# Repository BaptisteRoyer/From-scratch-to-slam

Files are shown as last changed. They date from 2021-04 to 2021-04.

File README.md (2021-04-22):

# From Scratch to SLAM

From scratch to SLAM est un projet open Source, créé par 4 étudiants de Junia ISEN. Dans ce repository vous trouverez tous les documents nécessaires afin de faire fonctionner votre robot.

Il est nécessaire pour tout commencer de télécharger le fichier notice.pdf.

Voici comment sont rangés nos fichiers :

- Dans le dossier Électronique, vous trouverez tout ce qui concerne les PCBs, le schéma électrique, et les datasheets des différents composants du projet
- Dans le dossier Pièces 3D, vous trouverez les fichiers 3Ds bruts des différents composants, cela vous permettra de redimensionner les différentes parties de votre robot.
- Dans le dossier Impression 3D, vous trouverez les fichiers stl à slicer, afin d'imprimer en 3D les pièces du robot.
- Dans le dossier Découpe Laser, vous trouverez tous les fichiers à découper, ce sont les plaques de plexiglass.
- Dans le dossier Software, vous trouverez des petits programmes de démonstration.

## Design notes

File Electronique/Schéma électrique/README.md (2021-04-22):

- La breadboard n'est pas représente sur le schéma (les pont en H sont branchés dessus ainsi que les masses de chaque bumper). 
- Le PCB couronne pour les capteurs IR n'est pas représenté sur le schéma.
- La batterie a les caractéristiques suivantes : 11.1 V, 5Ah, 50C.

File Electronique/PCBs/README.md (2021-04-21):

Vous trouverez dans ces dossiers les fichiers de conception (PCB et schémas électroniques)
et les fichiers d'impression (Gerber et NC Drill) des pièces PCB nécessaires aux bumpers et
aux capteurs IR.

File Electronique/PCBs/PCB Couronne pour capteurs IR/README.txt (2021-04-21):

La couronne pour les capteurs IR est divisée en deux, vous trouverez les deux parties dans ce dossier.

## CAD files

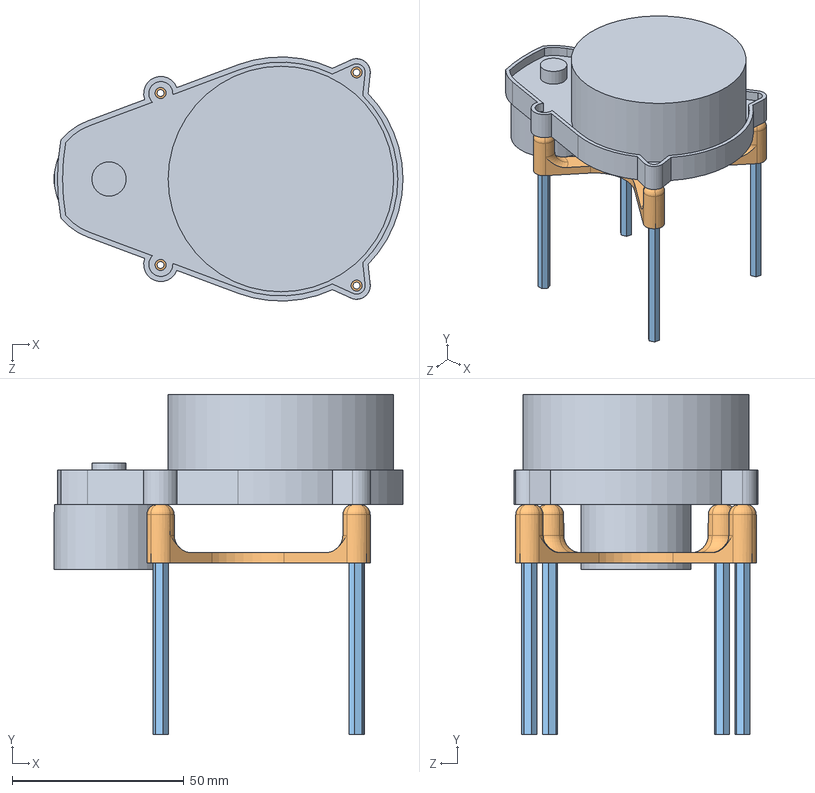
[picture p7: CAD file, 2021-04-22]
Pièces 3D/SolidWorks/lidar pilotis.SLDASM
101.5 x 99.0 x 70.9 mm
ydlidar x4
raccord lidar
support_hex60 x 4

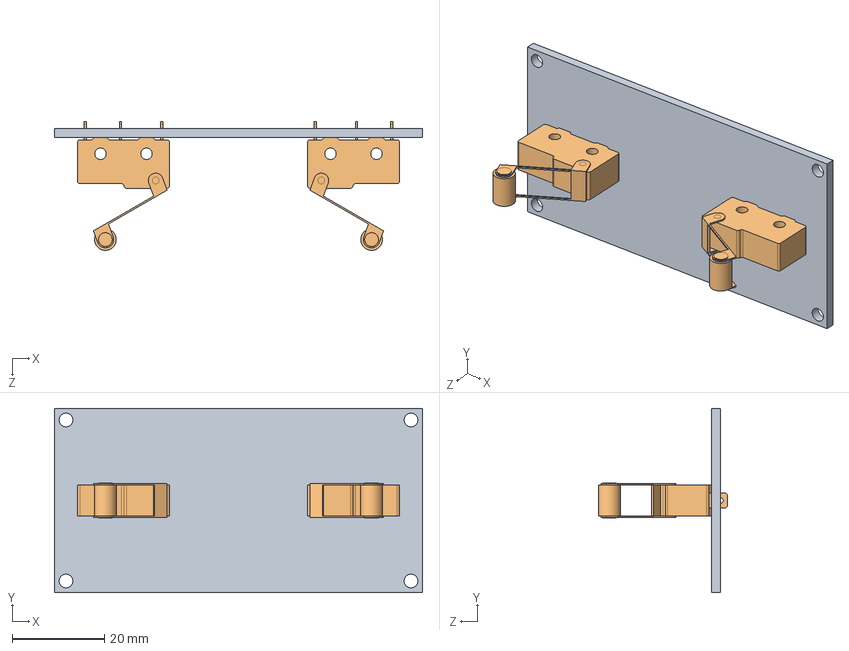
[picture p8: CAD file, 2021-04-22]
Pièces 3D/SolidWorks/pcb_bumper.SLDASM
80.0 x 40.0 x 28.0 mm
pcb_interrupteur
microswitch x 2

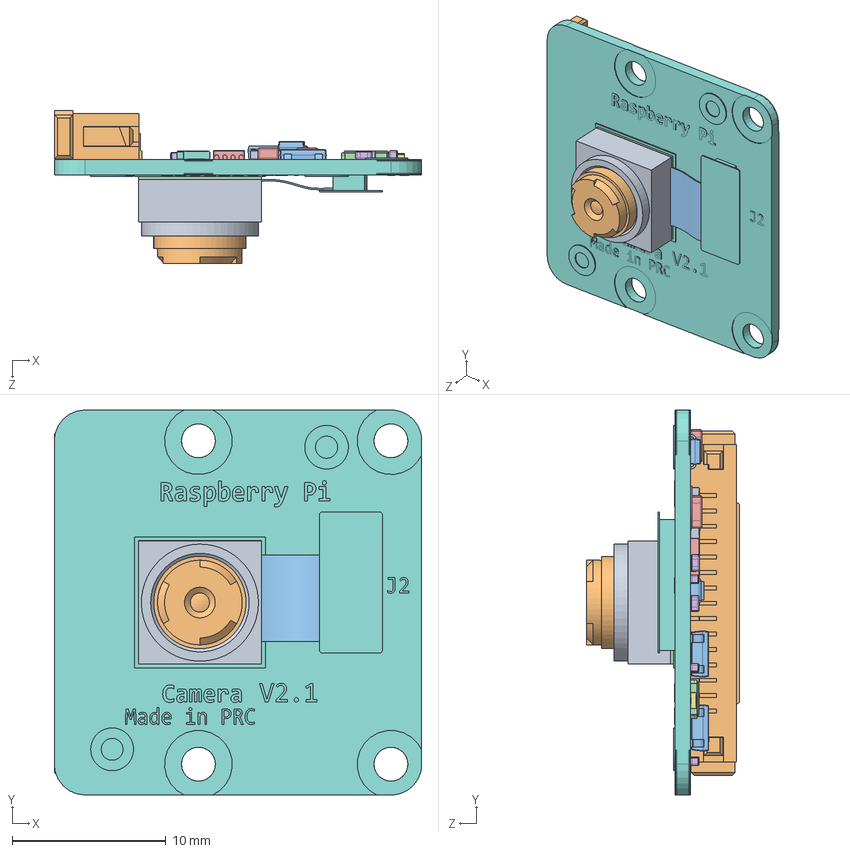
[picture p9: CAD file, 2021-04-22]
Pièces 3D/SolidWorks/RspCameraMia.SLDASM
23.9 x 25.0 x 9.96 mm
70521906_01.stp
70521906_02.stp
70521906_03.stp
70521906_04.stp
70521906_05.stp
70521906_06.stp
70521906_07.stp
PicameraPCB.stp
OVA5647_Housing.stp
OVA5647_Lens_FOV.stp
ribbon_cam.stp
CCD.stp
CAPC-0805-T0.75-BN.stp x 2
CAPC-0402-T0.55-BN.stp x 10
RESC-0402.stp x 3
RESC-0603.stp x 2
RESC-1210.stp
c-1-1734248-5-e-raspberry_display.stp
SOT23-5.stp x 3
KX7 SMD Quartz Crystal Resonator 3.2x2.5mm.stp
c6aaa.stp
4pin_smd.stp x 3

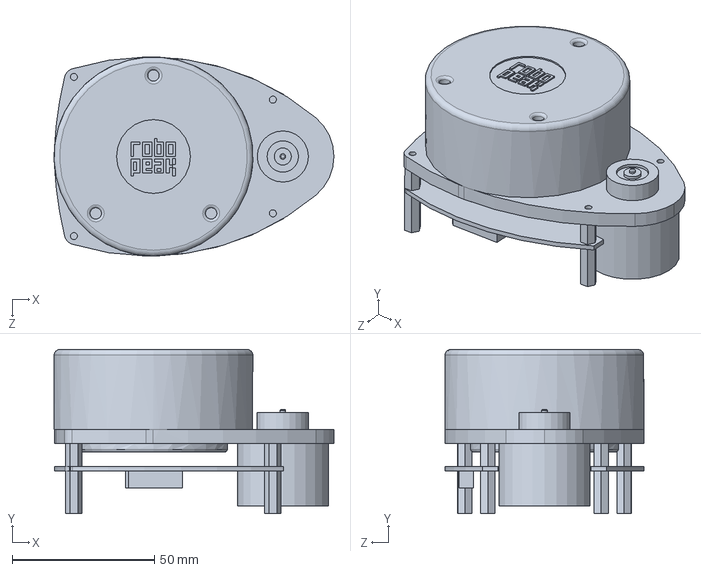
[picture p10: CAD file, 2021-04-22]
Pièces 3D/SolidWorks/rplidar_main.SLDPRT
98.5 x 57.7 x 70.0 mm

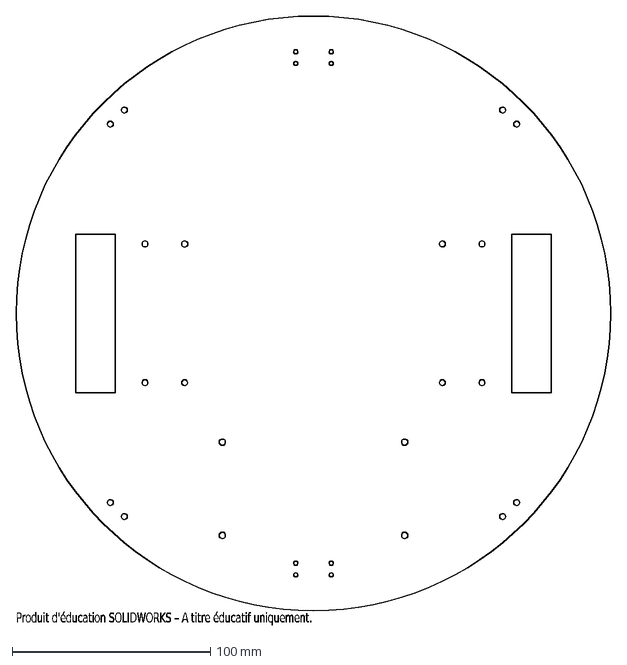
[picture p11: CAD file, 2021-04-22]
Découpe laser/base_300mm.DXF
Produit d'éducation SOLIDWORKS – A titre éducatif uniquement.

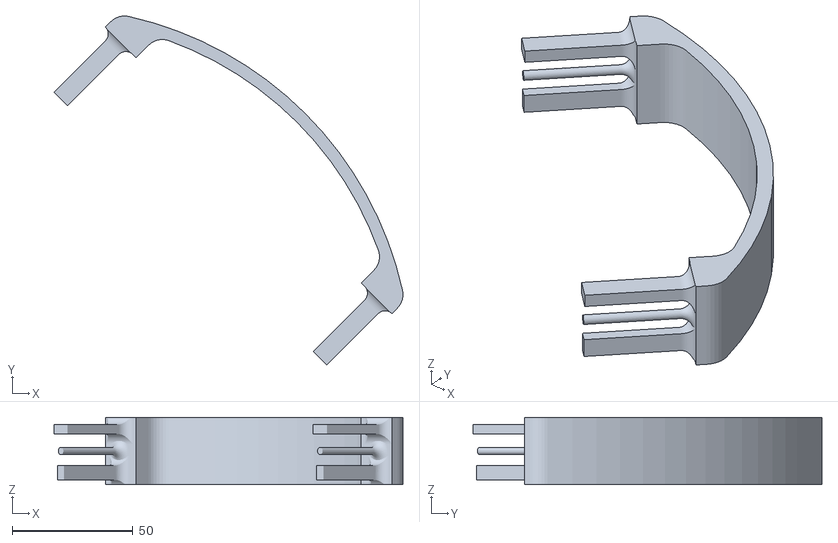
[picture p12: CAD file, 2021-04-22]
Impression 3D/bumper.STL
144.8 x 144.8 x 28.0

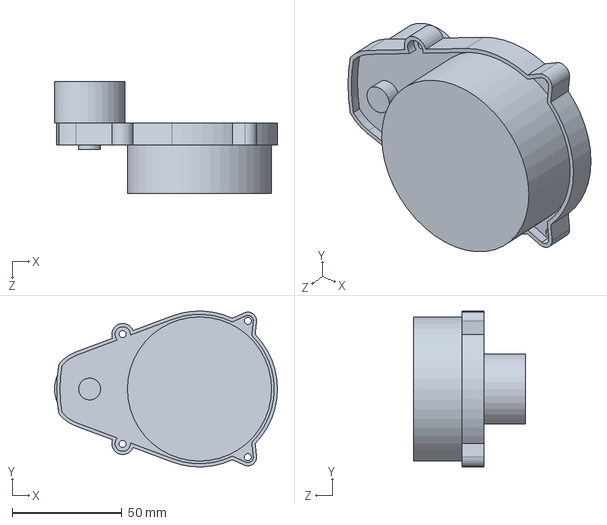
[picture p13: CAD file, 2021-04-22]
Pièces 3D/SolidWorks/ydlidar x4.SLDPRT
101.5 x 70.9 x 51.0 mm

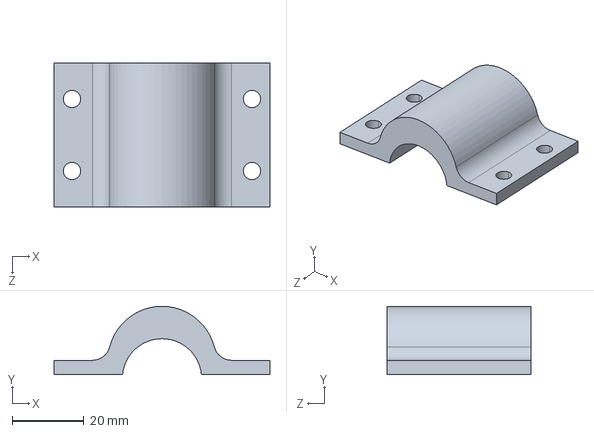
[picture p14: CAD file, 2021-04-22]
Pièces 3D/Step/mors_moteur_amovible.STEP
60.0 x 19.0 x 40.0 mm

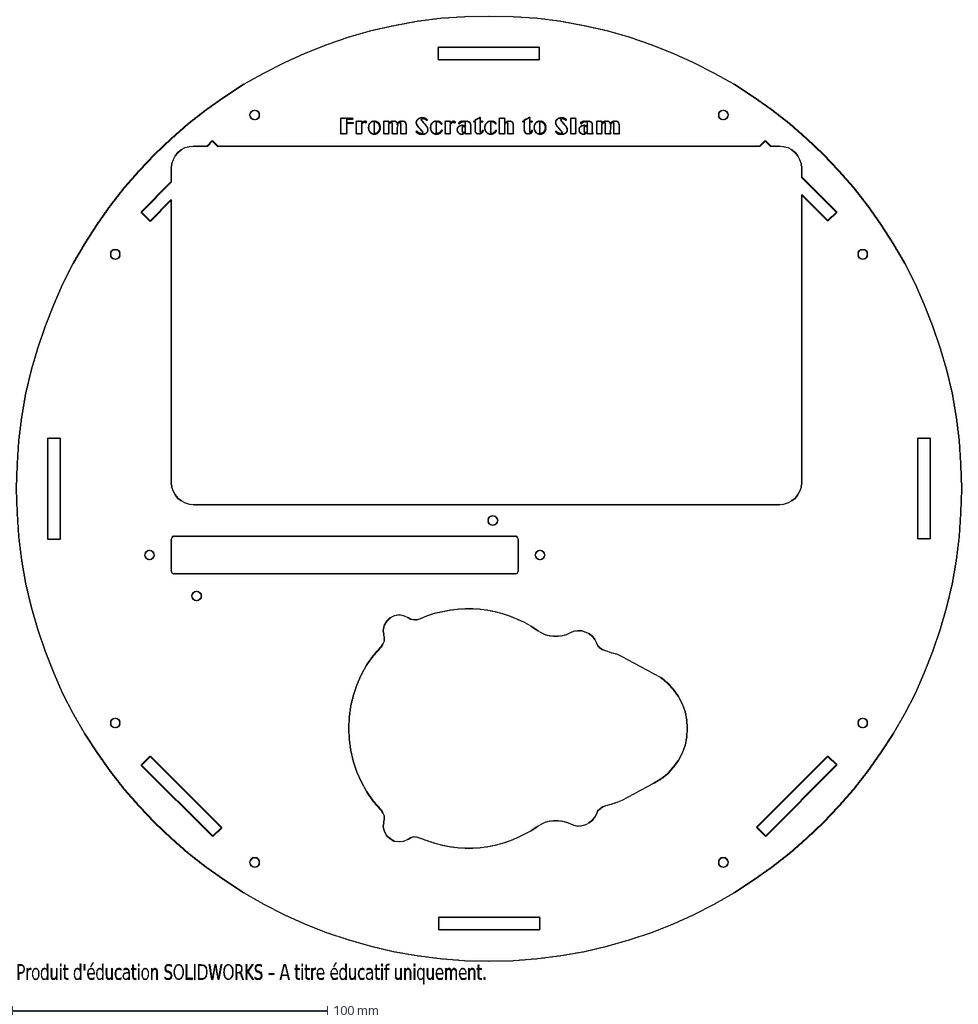
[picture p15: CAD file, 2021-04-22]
Découpe laser/capot.DXF
Produit d'éducation SOLIDWORKS – A titre éducatif uniquement.

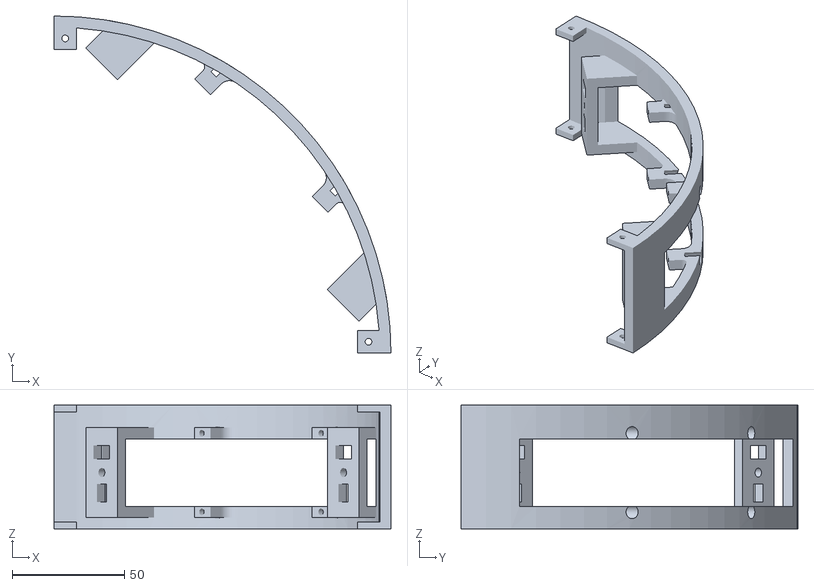
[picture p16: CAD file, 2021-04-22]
Impression 3D/paroi_bumper.STL
150.0 x 150.0 x 55.0

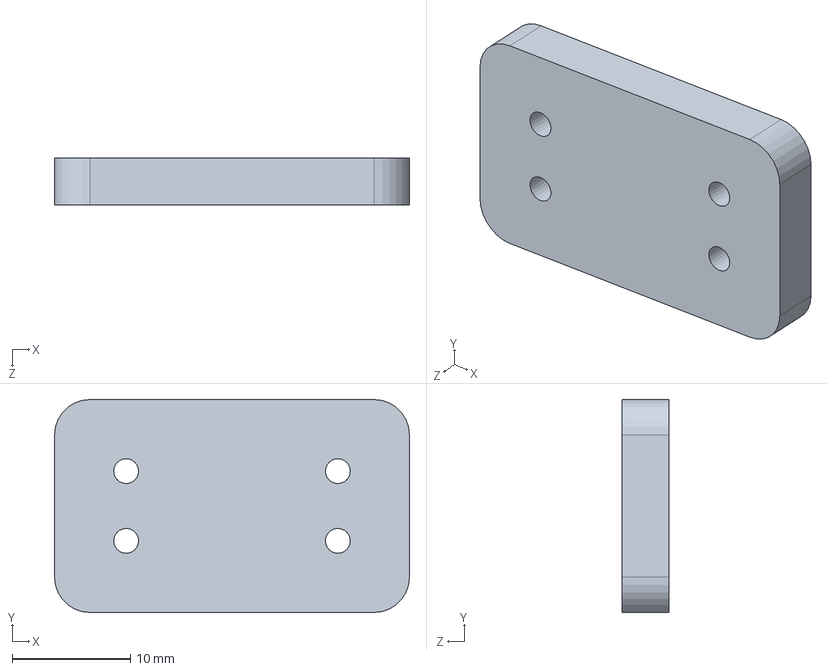
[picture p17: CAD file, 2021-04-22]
Pièces 3D/SolidWorks/support_roulement_a_bille.SLDPRT
30.0 x 18.0 x 4.00 mm

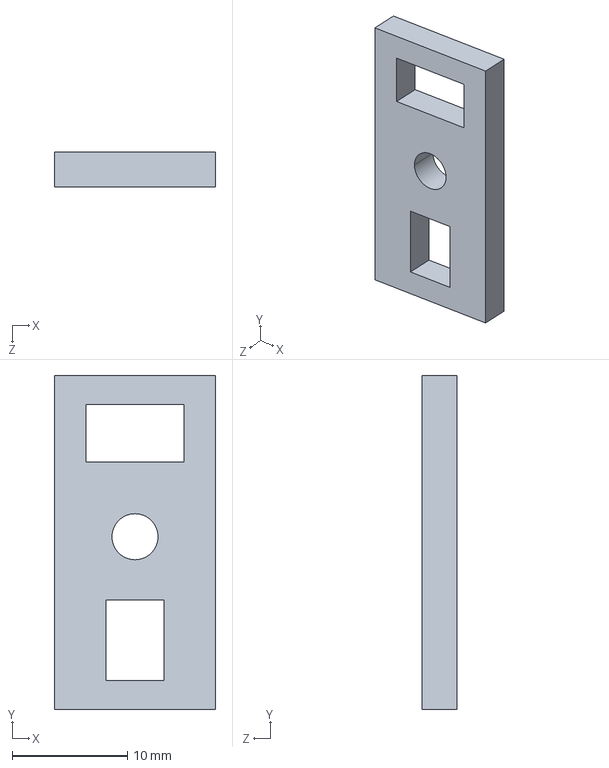
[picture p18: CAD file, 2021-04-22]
Pièces 3D/Step/bloqueur_bumper.STEP
14.0 x 29.0 x 3.00 mm

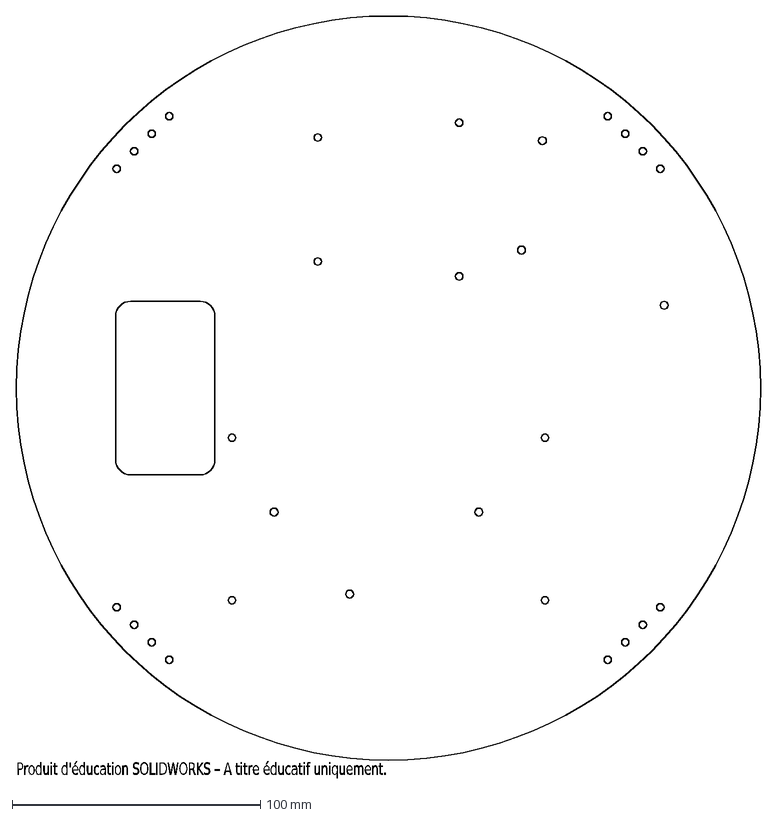
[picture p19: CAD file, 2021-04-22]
Découpe laser/support_cartes.DXF
Produit d'éducation SOLIDWORKS – A titre éducatif uniquement.

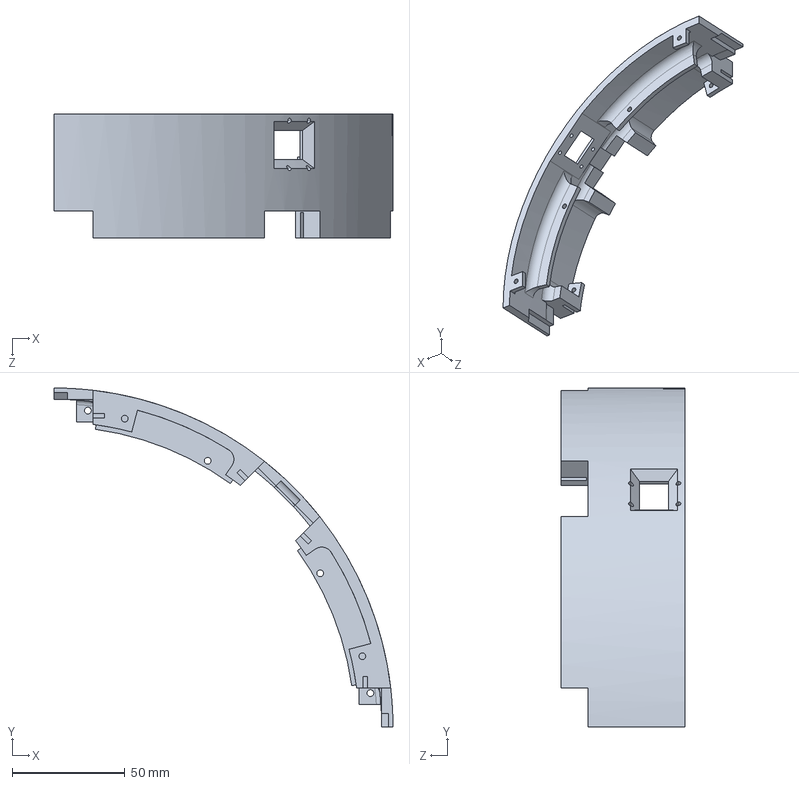
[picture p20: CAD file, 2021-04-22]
Pièces 3D/Step/quart_paroi_superieur_camera.STEP
150.0 x 150.0 x 55.0 mm

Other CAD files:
Pièces 3D/SolidWorks/raspberrypi_b_+_(assembly).SLDASM
Impression 3D/mors_moteur_amovible.STL
Impression 3D/mors_moteur_fixe.STL
Pièces 3D/SolidWorks/blindage_moteur.SLDPRT
Impression 3D/bloqueur_bumper.STL
Impression 3D/paroi_bouton.STL
Impression 3D/paroi_camera.STL
Impression 3D/paroi_superieure_laterale.STL
Impression 3D/raccord lidar.STL
Impression 3D/support_hub_USB.STL
Pièces 3D/SolidWorks/Capteur IR.SLDPRT
Pièces 3D/SolidWorks/Capteur IR.STEP
Pièces 3D/SolidWorks/Capteur IR.x_t
Pièces 3D/SolidWorks/MPU 6050 IMU.STEP
Pièces 3D/SolidWorks/Raspberry Pi 3 Model B+ Reference Model.step
Pièces 3D/SolidWorks/Raspberry Pi Display V1.1.SLDASM
Pièces 3D/SolidWorks/Raspberry Pi Display V1.1.STEP
Pièces 3D/SolidWorks/Switch Button.SLDPRT
Pièces 3D/SolidWorks/base.SLDPRT
Pièces 3D/SolidWorks/batterie.SLDPRT
Pièces 3D/SolidWorks/bloqueur_bumper.SLDPRT
Pièces 3D/SolidWorks/bumper.SLDPRT
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

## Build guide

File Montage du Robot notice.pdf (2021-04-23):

FROM SCRATCH TO SLAM – ROYER / MAERTEN / CANDUSSO / HAGUET | 1

# Notice d’assemblage

From Scratch to Slam

## Table des matières

## Liste du matériel :

- 3 plaques de plexiglas 32x32 cm minimum PMMA 5mm
- 1 bobine de plastique PLA
- Pack 100 boulons M3
- 8 vis auto-taraudeuses M4.8
- 12 boulons M2 nylon (boulon = ensemble vis + écrou)

Liste des composants & pièces :

1

er Etage :

- Base (plaque plexiglas)
- Carte Open UPS
- 2 moteurs Digilent 6V
- Batterie 12V
- 8 interrupteurs bumper
- 4 pcb interrupteurs bumper
- 4 parois bumper
- 4 bumpers
- 8 ressorts
- 2 modules mors moteur (pièce fixée à la base + pièce supérieure)
- 1 support de roue folle
- 1 roue folle (à bille)

2

e Etage :

- Support cartes (plaque plexiglas)
- 2 cartes Arduino Due
- ½ breadboard
- 2 hacheurs
- IMU
- Lidar
- Raccord lidar
- 8 colonnettes 55 mm
- Carte Raspberry Pi 4 model B
- Caméra RPi 8 Mpixels
- 8 capteurs IR
- Couronne PCB capteurs IR (2 pièces)
- Ecran tactile RPi 7 pouces
- 1 paroi supérieure caméra
- 1 paroi supérieure boutons
- 2 parois supérieures latérales
- Capot (plaque plexiglas)

## 1. Arborescence

Les fichiers sont enregistrés comme suit dans le Github du projet.

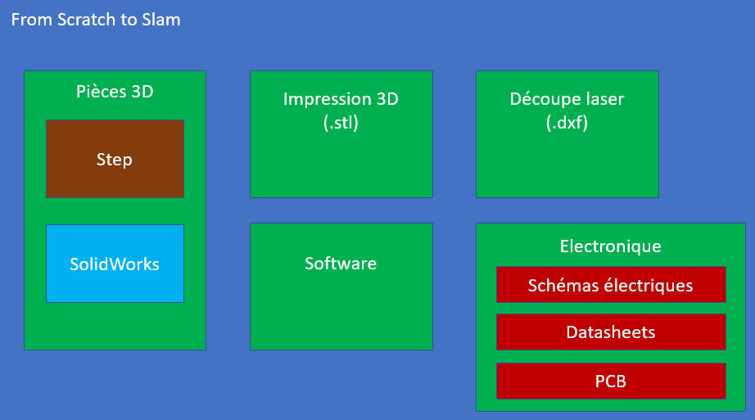
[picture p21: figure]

Les pièces 3D sont enregistrées au format .step et au format .sldprt (Solidworks 2019) pour pouvoir les ouvrir selon le logiciel de CAO utilisé. A noter : on ne peut pas ouvrir une pièce Solidworks éditée sur une version future.

### 1. Impression 3D

Les fichiers d’impression sont enregistrés au format .stl pour les ouvrir sur un logiciel d’impression 3D (ex. PrusaSlicer). On place les pièces sur le logiciel de manière optimale (pour éviter trop de supports et prendre le moins de temps d’impression) puis on en retire un fichier .gcode que l’imprimante lit.

### 2. Découpe laser

Les fichiers de découpe sont enregistrés au format .dxf pour les ouvrir sur un logiciel de découpe laser (ex. Job control Trotec). On détermine l’ordre de tracé du laser sur le logiciel et on lance la découpe.

Tous les fichiers concernant les schémas électriques et les PCB correspondants sont dans le dossier Electronique ainsi que les datasheets des composants utilisés.

## 2. Assemblage

Pour imprimer, découper et assembler le robot, on partira du bas vers le haut car on souhaite mettre en œuvre en premier les commandes moteur. Aussi on a choisi de coller les écrous sur les parois afin de visser plus facilement.

1. Découper au laser la base.dxf dans le dossier Découpe laser.

& imprimer dans le dossier impression 3D

- 2 mors_moteur_fixe.stl
- 2 mors_moteur_amovible.stl
- 4 bumpers.stl
- 4 paroi_bumper.stl
- 8 bloqueur_bumper.stl
- 1 support_roulement_a_bille.stl

& découper les PCB interrupteurs

2. Souder les interrupteurs sur les PCB correspondants
3. Visser les PCB interrupteurs sur les parois

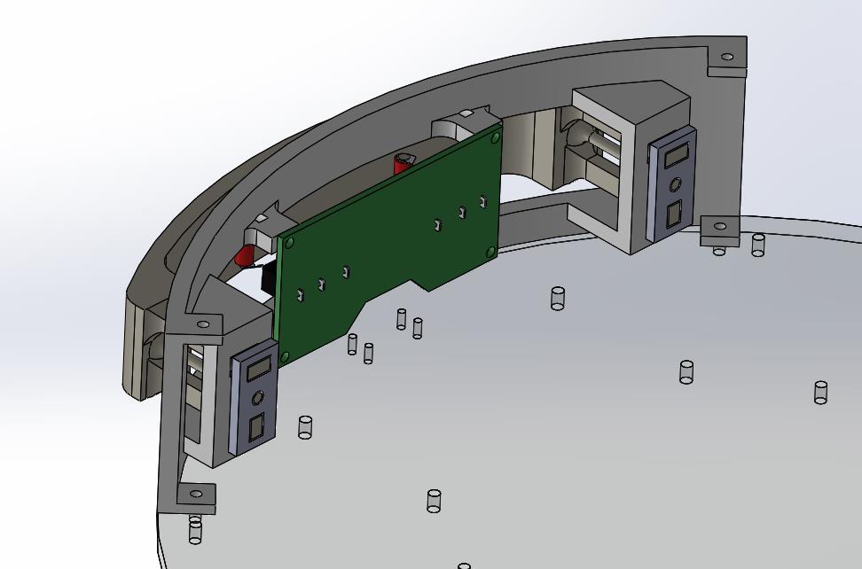
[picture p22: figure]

Figure 1 assemblage paroi bumper bloqueur et PCB interrupteur

4. Placer les ressorts sur les bumpers et les assembler sur les parois puis coller les bloqueurs sur les bumpers de sorte que les interrupteurs effleurent les bumpers.

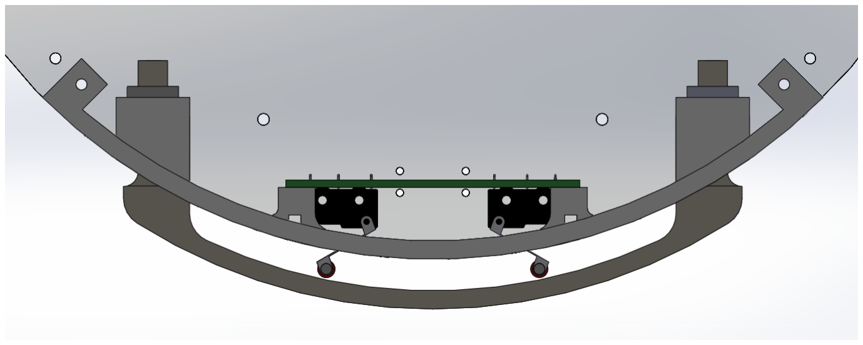
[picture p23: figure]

Figure 2 Assemblage bumper

5. Assembler les mors moteur en y insérant les moteurs digilent 6V (limer légèrement au besoin & 8 vis auto-taraudeuses M4.8)
6. Visser la roue folle et le support contre la base (4 vis nylon et écrou métal M2)
7. Visser les mors moteurs sur la base (8 boulons M3)
8. Visser la carte Open UPS (8 boulons M3)
9. Visser les parois bumper assemblées (8 boulons M3)
10. Câbler la batterie à la carte Open UPS
11. Câbler le bouton poussoir à la carte Open UPS
12. Découper le support_carte.dxf et le capot.dxf dans le dossier Découpe laser

& imprimer dans le dossier Impression 3D

- 2 paroi_laterale.stl
- 1 paroi_camera.stl
- 1 paroi_bouton.stl
- 1 support_hub_USB.stl
- 1 raccord_lidar.stl
13. Visser la caméra sur la paroi correspondante (4 vis nylon et écrou métal M2)
14. Visser les 2 cartes Arduino Due sur la plaque support carte (6 boulons M3)
15. Visser le lidar au raccord lidar (vis M2.4)
16. Visser les 4 colonnettes au raccord lidar
17. Visser les 4 colonnettes à l’écran (pas à fond)
18. Visser la carte Raspberry Pi 4 model B en dessous de l’écran
19. Visser l’écran et le lidar sur le support carte (8 vis M3)
20. Visser la paroi caméra sur le support carte, opposée au trou de passage des câbles (2 boulons M3)
21. Visser le bouton poussoir sur la paroi bouton
22. Coller la borne de chargement et le bouton switch sur la paroi bouton
23. Visser la paroi bouton et les 2 parois latérales (6 boulons M3)

24. Souder les capteurs IR sur la couronne PCB
25. Visser la couronne PCB sur les supports des parois (8 boulons M3) et insérer les capteurs dans leurs encoches respectives sur les parois
26. Inclure l’IMU sur la breadboard ainsi que les 2 hacheurs
27. Câbler selon le schéma électrique de câblage situé dans le dossier schéma électrique

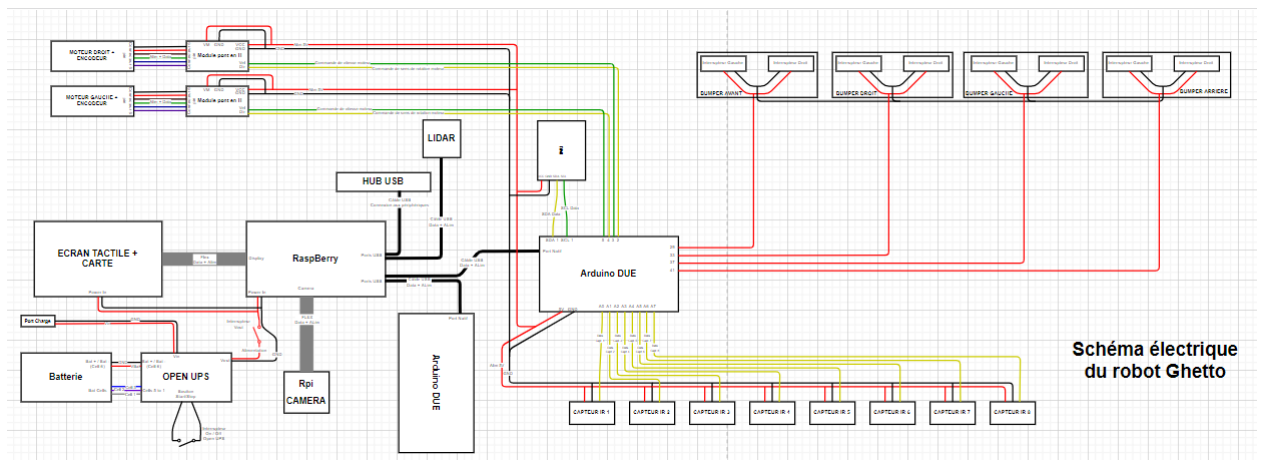
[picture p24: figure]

Figure 3 Schéma électrique du robot

28. Visser le capot sur le robot une fois le câblage terminé (8 boulons M3)

## 3. Paramétrage et installation de l’Open UPS

La carte Open UPS permet de brancher une batterie quelconque et d’avoir en sortie une tension voulue. Dans notre cas, nous avons une batterie 11.1 V, 5000 mAh, 50C, et une tension de sortie
de | | | | | 5.25 | | | | V.
La | carte | est | paramétrable | à | l’aide | d’un | software | disponible | ici :
http://resources.mini-box.com/online/PWR-OpenUPS/software/OpenUPS-installer.exe

Le software se décompose en trois parties : l’onglet « status » et l’onglet « settings » qui contient l’onglet « battery wizard ». Le premier onglet permet le suivi des paramètres de la carte, tandis que les deux autres permettent de paramétrer la carte.

### 1. L’onglet « status »

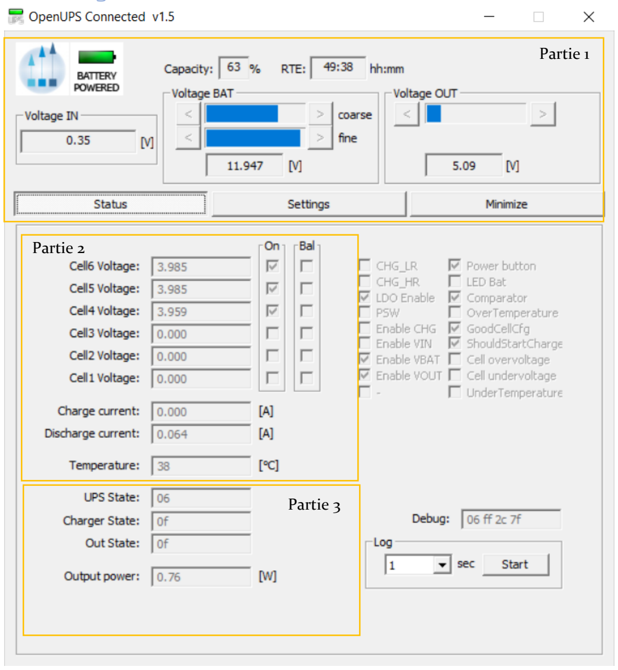
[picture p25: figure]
Partie 1; Partie 2; Partie 3

On peut retrouver dans cet onglet certaines données concernant la batterie et la carte. On peut le diviser en 3 parties comme défini sur la capture d’écran ci-dessus.

La première partie concerne les données principales de la batterie, à savoir la capacité restante, le temps restant estimé de décharge, la tension d’entrée si la carte est branchée au secteur, la tension de sortie de la batterie, et la tension de sortie de la carte Open UPS. On peut retrouver cette partie également dans l’onglet « settings »

La deuxième partie concerne la tension de chaque cellule de la batterie (jusqu’à 6 cellules) ainsi que le courant de charge ou décharge de la batterie.

Pour finir, la troisième partie concerne les données de la carte, à savoir l’état de la carte (allumée, éteinte, en veille, etc…), l’état de la charge de la batterie (la batterie est en charge ou en décharge), et enfin l’état de la sortie de la carte (si la carte délivre ou non une tension de sortie). On trouve également la puissance de sortie de la carte dans cet onglet.

### 2. L’onglet « settings »

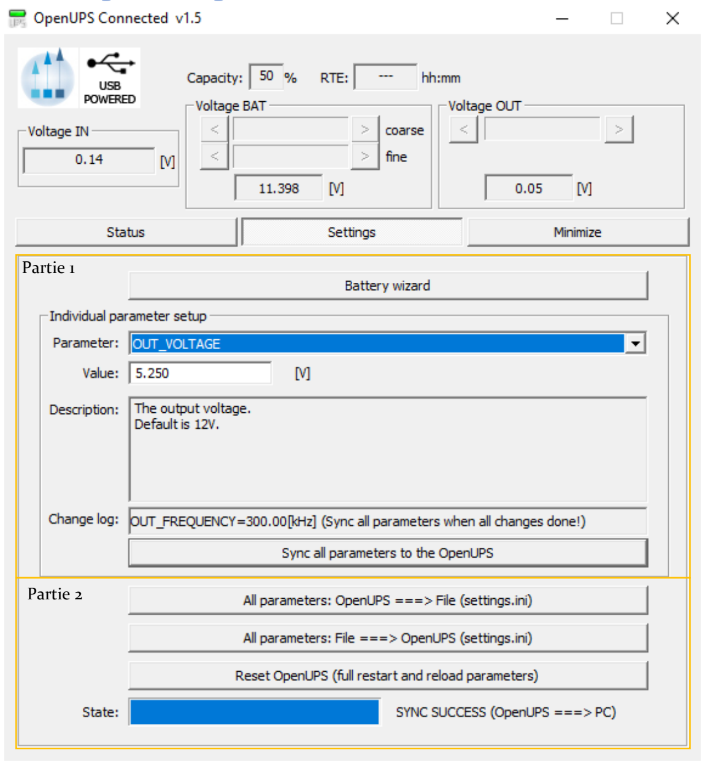
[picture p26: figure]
Partie 1; Partie 2

On peut retrouver dans cet onglet tous les paramètres de la carte que l’on peut modifier. Il est important de noter que le constructeur déconseille aux utilisateurs novices de modifier ces paramètres, ce qui pourrait détruire la carte ou les composants branchés en sortie. On peut diviser cet onglet en deux parties suivant la capture d’écran ci-dessus.

La première partie permet de modifier les paramètres de la carte. « Parameter » permet de sélectionner le paramètre à modifier (le plus important étant OUT_VOLTAGE), et Value permet de modifier la valeur de celui-ci. On a également la description du paramètre qui contient la valeur par défaut de celui-ci, ainsi que le « changelog » qui donne les changements que l’utilisateur à amorcer. Le bouton « Sync all parameters to the OpenUPS » permet de confirmer les changements et les appliquer à la carte Open UPS.

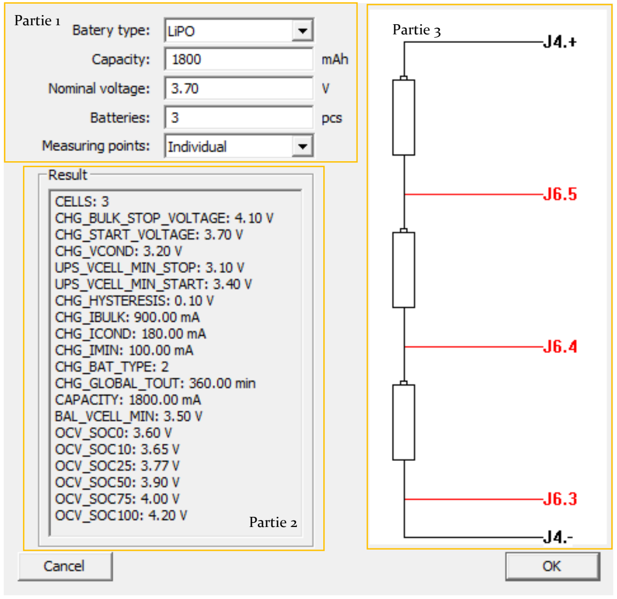
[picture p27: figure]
Partie 1; Partie 2; Partie 3

FROM SCRATCH TO SLAM – ROYER / MAERTEN / CANDUSSO / HAGUET | 10

La deuxième partie permet avec le bouton « All parameters : OpenUPS ===> File (settings.ini) » de récupérer les paramètres de la carte OpenUPS vers le software, ou inversement avec le bouton « All parameters : File (settings.ini) ===> OpenUPS » d’envoyer les paramètres modifiés du software vers la carte OpenUPS. Le dernier bouton « Reset OpenUPS (full restart and reload parameters) » permet de reboot la carte et ainsi d’appliquer les nouveaux paramètres.

Ainsi, pour modifier un paramètre, il faut sélectionner le paramètre, le modifier, synchroniser les changements avec la carte, envoyer les paramètres modifiés du software vers la carte pour être sûr du téléversement, et reboot la carte OpenUPS.

### 3. L’onglet « Battery wizard »

Cet onglet permet de paramétrer très simplement la carte OpenUPS en entrant le type de batterie. On peut le diviser en trois parties suivant la capture d’écran ci-dessus.

FROM SCRATCH TO SLAM – ROYER / MAERTEN / CANDUSSO / HAGUET | 11

La première partie permet de définir le type de batterie en indiquant le type de batterie (Li-ion, LiPo ou LIFEPO4), la capacité de la batterie (en mAh), la tension de chaque cellule de la batterie (en V), et le nombre de ces cellules.

La deuxième partie liste tous les paramètres et leurs valeurs modifiés selon le type de batterie entrée dans la partie précédente. On y retrouve le nombre de cellules (CELLS), la capacité (CAPACITY) et le type de la batterie (CHG_BAT_TYPE), à vérifier pour ne pas avoir d’erreur. Tous ces paramètres sont modifiables ultérieurement dans l’onglet « settings ».

La dernière partie est un schéma montrant les connexions à faire entre la batterie et la carte OpenUPS. La première cellule est toujours connectée à la pin J4.+ qui correspond à Bat +. Les autres cellules se branchent sur la pin J6 de la manière suivante : la cellule 2 sur J6.5, la cellule 3 sur J6.4, la cellule 4 sur J6.3 etc… La masse se branche sur le prochain pin disponible après les cellules. Dans notre exemple, on a une batterie avec 3 cellules. Ainsi, la première est branchée sur J4.+, la deuxième sur J6.5, la troisième sur J6.4, et la masse sur J6.3 (se référer au schéma électrique sur GitHub dans l’onglet Electronique/Schéma électrique/Schéma électrique.pdf).

### Conclusion

L’installation d’une carte OpenUPS est simplifiée grandement par le software. Ainsi, pour intégrer une carte à un circuit électrique, il faut suivre les points suivants :

- Installer le software OpenUPS Configuration
- Utiliser l’onglet « battery wizard » pour paramétrer la carte.
- Utiliser l’onglet « settings » pour modifier le paramètre OUT_VOLTAGE qui est la tension de sortie de la carte.
- Brancher la batterie selon le schéma disponible dans l’onglet « battery wizard ».

La carte est maintenant prête à être utilisée dans le circuit.

Vous pouvez trouver les manuels officiels et le schéma des pins de la carte dans le GitHub dans l’onglet Electronique/Datasheets/Open UPS. Le manuel « Open UPS Hardware Manual » contient notamment tous les paramètres modifiables dans l’onglet settings, et le fichier « Open UPS 2D Drawings » contient la disposition des différents pins sur la carte.

FROM SCRATCH TO SLAM – ROYER / MAERTEN / CANDUSSO / HAGUET | 12

## 4. Utilisation de l’Open UPS

Une fois la carte Open UPS paramétrée et branchée (se référer au paragraphe « Paramétrage et installation de l’Open UPS ») elle est prête à être utilisée.

### 1. Démarrage

Pour démarrer la carte Open UPS, il suffit de connecter les deux pins du connecteur « start/stop button » (voir figure 1) pendant 1 seconde. Dans notre cas, nous avons connecter ces deux pins à un bouton poussoir (bouton vert sur la paroi arrière du robot). Il suffit ainsi d’appuyer sur ce bouton pendant 1 seconde pour démarrer la carte, mais une simple connexion avec un objet métallique pou des tests sur une carte sans bouton.

### 2. Utilisation

Une fois la carte Open UPS paramétrée et branchée, elle fonctionne seule et n’a besoin d’aucune intervention ou interface extérieure. La LED MAIN permet de vérifier l’état de la carte selon les points suivants (traduction des points donnés dans le Hardware manuel disponible dans le GitHub dans l’onglet Electronique/Datasheets/Open UPS) :

1) 5 x (30ms ON,30ms OFF) clignotement rapide de 750ms de période : délai initial (démarrage).
2) 500ms ON, 500ms OFF : L’UPS est en attente des bonnes conditions pour démarrer. Elle restera dans cet état si l’une des conditions suivantes est respectée : mauvaise configuration de la batterie ou tension de cellule trop faible et pas de tension d’entrée.
3) ON constant : l’UPS est alimentée par la tension d’entrée (secteur).
4) 500msec ON, 2.5 sec OFF : l’UPS est alimentée par la tension de la batterie.
5) 1 sec ON, 1 sec OFF : OFFDELAY (temps entre lequel une condition d’arrêt de la carte a été remplie (Sous tension par exemple) et le signa d’arrêt est envoyé à la carte) géré par le paramètre UPS_VBAT_UVP_OFF_TOUT.
6) 3x (500ms ON,500ms OFF) + 3 sec OFF (répété) : délai Hardware OFF (temps entre lequel le signal d’arrêt de la carte est envoyé et la coupure de la tension de sortie) géré par le paramètre UPS_HARDOFF_TOUT (paramétrable grâce au software Open UPS Configuration), une fois ce délai passé la carte entrera en veille.

La LED BATTERY permet de vérifier l’état de la batterie selon les points suivants (traduction des points donnés dans le Hardware manuel disponible dans le GitHub dans l’onglet Electronique/Datasheets/Open UPS) :

1) Clignotement rapide : Mauvaise configuration des cellules ou mauvaises connexions de ces dernières sur la carte (se référer au paragraphe « Paramétrage et installation de l’Open UPS »).

FROM SCRATCH TO SLAM – ROYER / MAERTEN / CANDUSSO / HAGUET | 13
2) 1 sec ON, 1 sec OFF (répété) : la batterie se charge.
3) ON constant : la batterie est complètement chargée.

4 OFF constant (avec la LED MAIN dans l’état 500 ms ON, 2.5 sec OFF) : la carte utilise la batterie comme alimentation.

### 3. Extinction

Pour éteindre l’UPS, il suffit de connecter les deux pins du connecteur « start/stop button » pendant 5 secondes. Cela envoie un signal d’arrêt à la carte et on passe dans l’état 6) de la MAIN LED (voir paragraphe « 2. Utilisation »). Une fois le délai passé la carte passera en mode veille et peut être déconnectée de toute source d’alimentation en toute sécurité.

FROM SCRATCH TO SLAM – ROYER / MAERTEN / CANDUSSO / HAGUET | 14

## 5. Démarrage et extinction du robot

### 1. Mise en marche

D’abord il faut démarrer l’Open UPS. Pour cela, maintenez le bouton vert pendant environ deux secondes. Ensuite, démarrez le Raspberry en mettant l’interrupteur en position ON. Voilà, le robot est démarré.

### 2. Démarrage des programmes

Si vous souhaitez démarrer le programme de test, vous devrez démarrer le programme Arduino, et le programme Processing correspondant. Pour se faire :

1. Rendez-vous dans le dossier Processing Projects (sur le Bureau)
2. Ouvrez le dossier ProcessingGhetto
3. Lancez ProcessingGhetto.pde
4. Ouvrez le dossier Arduino Projects (sur le Bureau)
5. Rendez vous dans Outil > Port, et vérifiez le numéro du port de votre Arduino, normalement elle se présente sous la forme ttyACMn, ou n est un entier.
6. Rendez vous à la ligne 17 du programme Processing, et remplacez le numéro de port correspondant dans la partie « /dev/ttyACMn ».
7. Téléversez le programme Arduino
8. Téléversez le programme Processing.

Si cela ne fonctionne pas, vérifiez que vous avez bien téléversé sur le bon port, si ce n’est pas le cas, changez de port sur Arduino, et changez à nouveau la ligne 17 sous processing.

Si vous souhaitez coder vos propres programmes Arduino, vérifiez bien que vous avez bien téléchargé, et inclus les fichiers Wheels.cpp et Wheels.h.

Les fichiers se trouvent aussi dans le dossier « software » du GitHub

### 3. Éteindre le robot

Pour se faire :

1. Eteignez la raspberry PI en mettant l’interrupteur sur la position OFF
2. Eteignez l’Open UPS en maintenant le bouton vert jusqu’à ce que la led MAIN clignotte 3 fois.

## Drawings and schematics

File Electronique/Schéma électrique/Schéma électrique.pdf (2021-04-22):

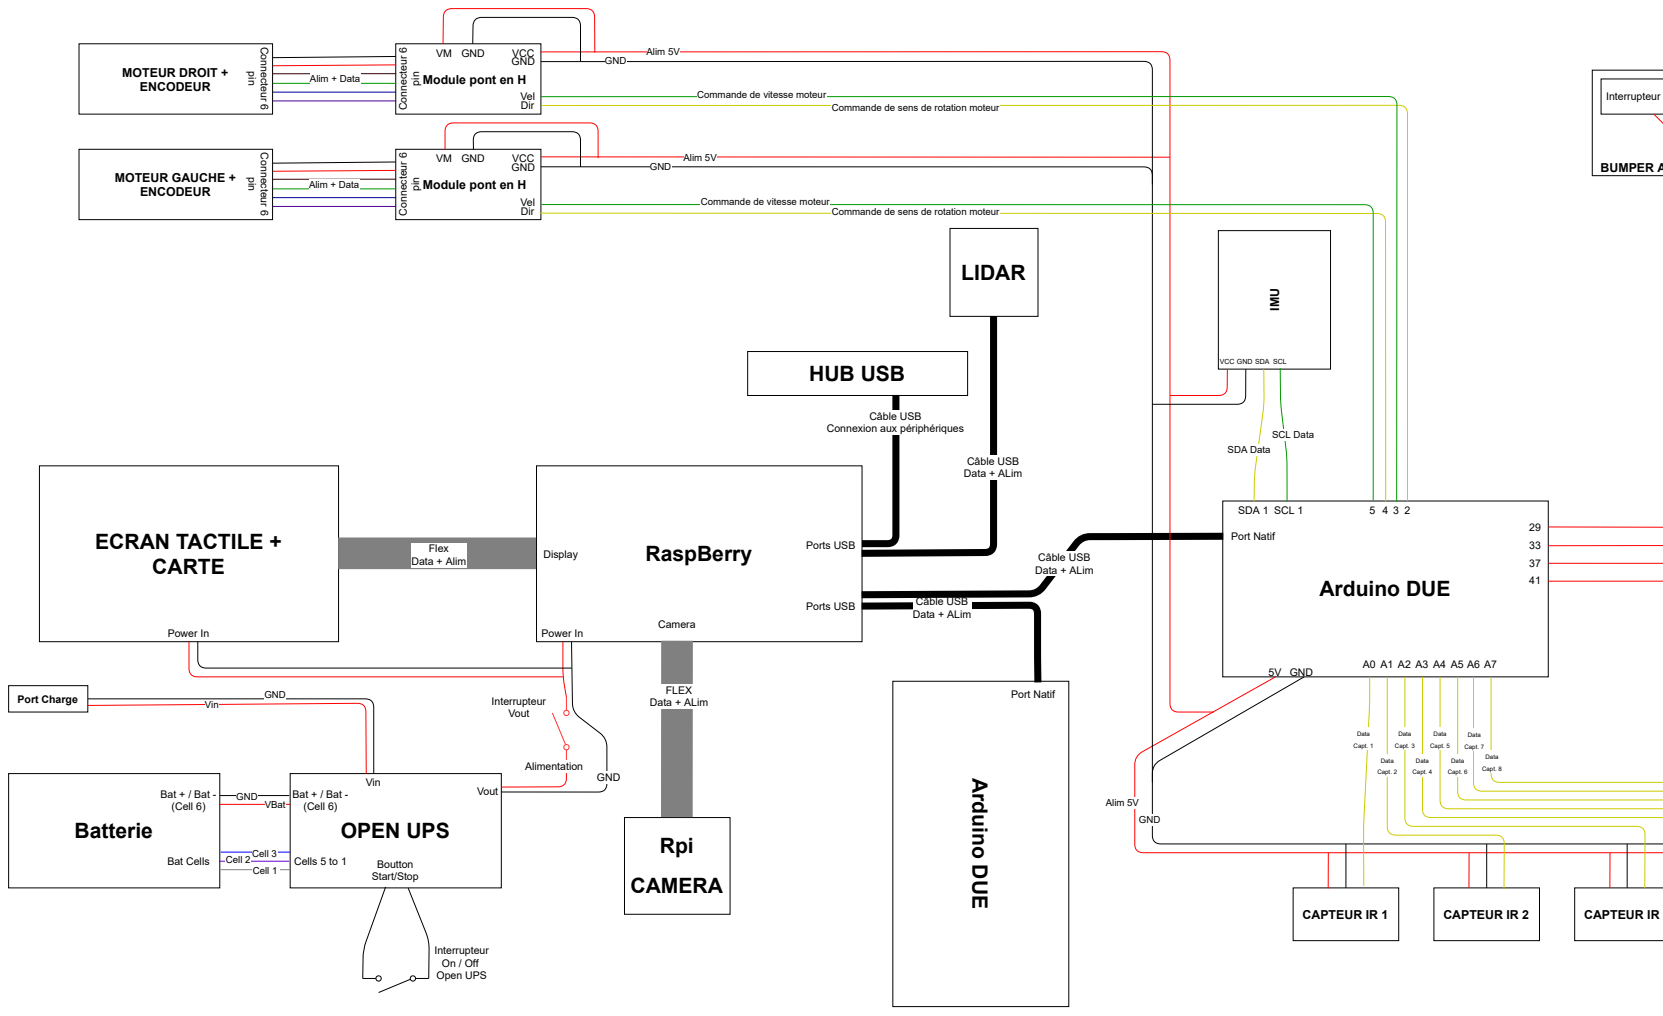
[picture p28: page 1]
Batterie; OPEN UPS; Bat Cells; Bat + / Bat - (Cell 6); Cells 5 to 1; GND; VBat; Cell 2 Cell 3; Cell 1; Vin; Port Charge; Vout; Alimentation; Interrupteur Vout; Boutton Start/Stop; Interrupteur On / Off Open UPS; Power In; Rpi; CAMERA; Camera; FLEX Data + ALim; Flex Data + Alim; HUB USB; Câble USB; Câble USB Data + ALim; Display; Ports USB; Arduino DUE; Port Natif; CAPTEUR IR 1; Alim 5V; 5V GND; CAPTEUR IR 2; CAPTEUR IR; MOTEUR DROIT + ENCODEUR; MOTEUR GAUCHE + ENCODEUR; VCC GND; Dir; Vel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

Connecteur 6
Module pont en H

Commande de vitesse moteur

Commande de sens de rotation moteur

LIDAR Arduino DUE

VCC GND SDA SCL

Connexion aux périphériques

RaspBerry ECRAN TACTILE +
CARTE

Data + ALim Ports USB

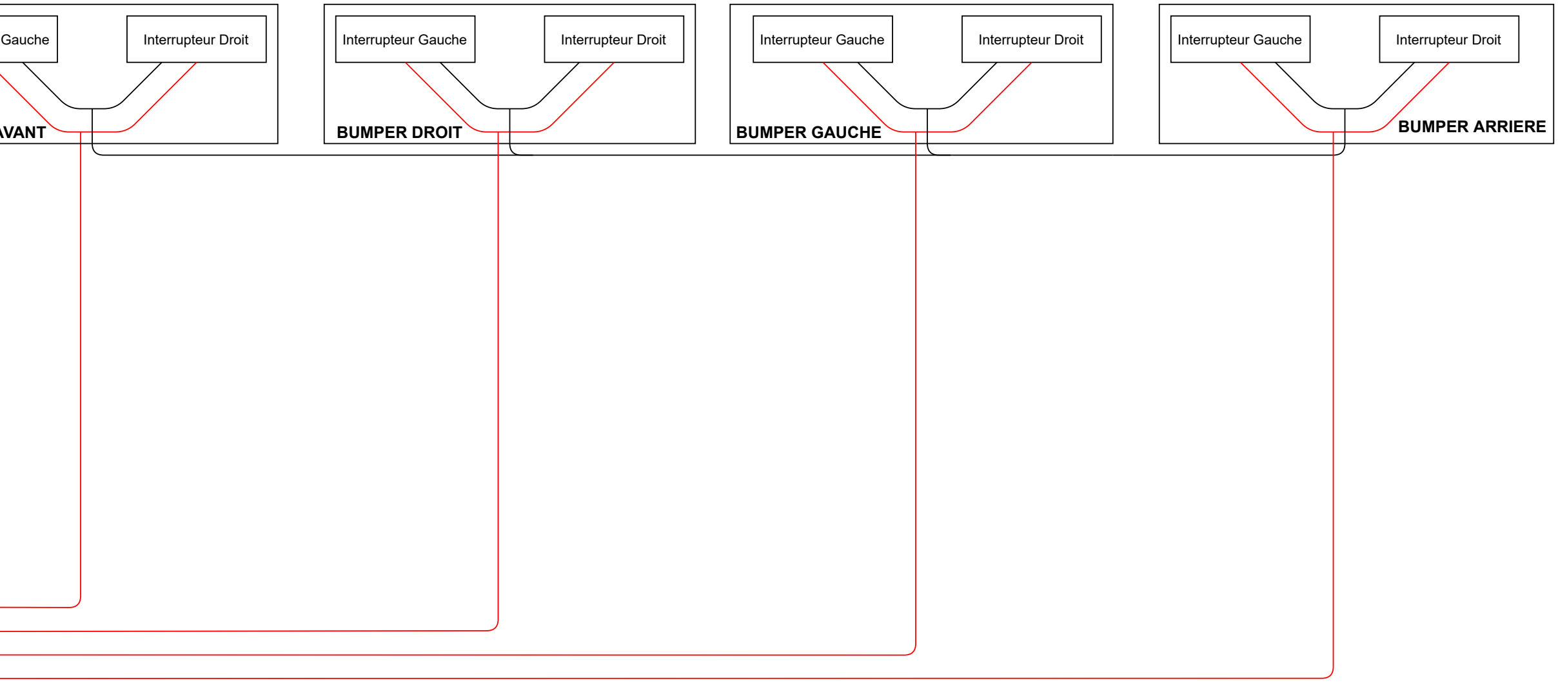
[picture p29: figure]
Gauche; Interrupteur Droit; AVANT; Interrupteur Gauche; BUMPER DROIT; BUMPER GAUCHE; BUMPER ARRIERE
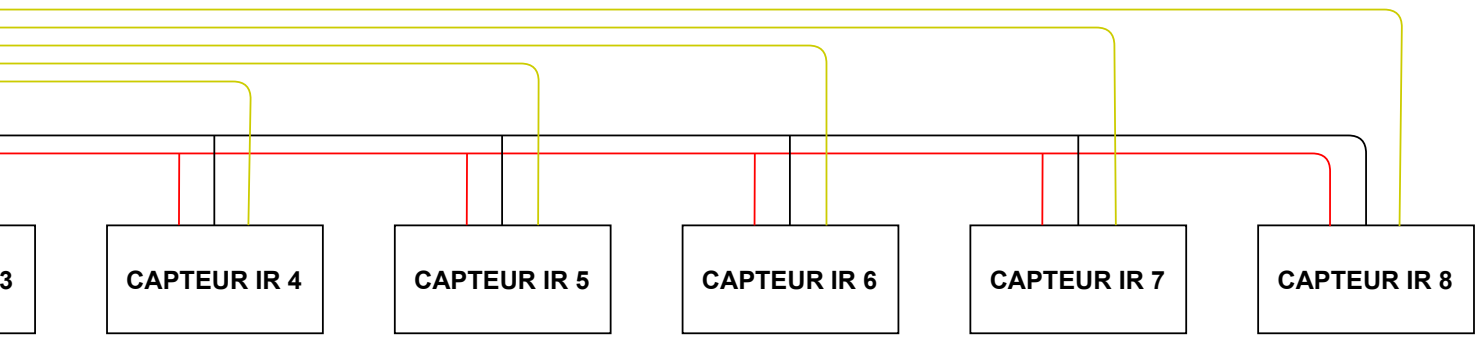
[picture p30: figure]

CAPTEUR IR 4 | CAPTEUR IR 5 | CAPTEUR IR 6 | CAPTEUR IR 7 | CAPTEUR IR 8

# Schéma électrique du robot Ghetto

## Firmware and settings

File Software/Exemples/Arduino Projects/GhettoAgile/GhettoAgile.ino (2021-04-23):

#include <Wheel.h>

#define DIR_R 3
#define DIR_L 5
#define EN_R 2
#define EN_L 4

Wheel rightWheel(DIR_R, EN_R);
Wheel leftWheel(DIR_L, EN_L);

void setup() {
  Serial.begin(9600);
  rightWheel.wSetup();
  leftWheel.wSetup();
}

void loop() {
  if (Serial.available() > 0)
  {
    char val = Serial.read();
    switch (val)
    {
      case 'z':
        goForward();
        break;
      case 'q':
        goLeft();
        break;
      case 's':
        goBack();
        break;
      case 'd':
        goRight();
        break;
      case 'x':
        goStop();
        break;
      case 'c':
        Serial.println("Go Square");
        for (int i = 0; i < 4; i++) {
          goForward();
          delay(2000);
          goLeft();
          delay(1000);
        }
        goStop();
        break;
      case 'o':
        Serial.println("Go Circle");
        rightWheel.setSpd(210);
        leftWheel.setSpd(180);
        delay(3000);
        goStop();
        break;
      default:
        break;
    }
  }
}

//FONCTIONS DE DEPLACEMENT
void goForward() {
  rightWheel.setDir(LOW); leftWheel.setDir(HIGH);
  rightWheel.setSpd(200); leftWheel.setSpd(200);
}
void goRight() {
  rightWheel.setDir(HIGH); leftWheel.setDir(HIGH);
  rightWheel.setSpd(200); leftWheel.setSpd(200);
}
void goLeft() {
  rightWheel.setDir(LOW); leftWheel.setDir(LOW);
  rightWheel.setSpd(200); leftWheel.setSpd(200);
}
void goBack() {
  rightWheel.setDir(HIGH); leftWheel.setDir(LOW);
  rightWheel.setSpd(200); leftWheel.setSpd(200);
}
void goStop() {
  rightWheel.setSpd(0);
  leftWheel.setSpd(0);
}

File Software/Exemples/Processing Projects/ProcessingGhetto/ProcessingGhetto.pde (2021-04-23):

import controlP5.*;
import processing.serial.*;

String val;     // Data received from the serial port
String inString;

Serial port;
ControlP5 cp5;
PImage bg;

void setup(){
  size(780,460);
  cp5 = new ControlP5(this);
  
  cp5.addButton("Carre").setPosition(50,20).setSize(100,100);
  cp5.addButton("Circle").setPosition(151,20).setSize(100,100);
  try{port = new Serial(this, "/dev/ttyACM0", 9600);}
  catch(Exception e){println("No port available");}
  port.bufferUntil(10);

  bg = loadImage("JuniaISEN.jpg");
}

void draw(){
  background(bg);
  //text("Direction souhaitée",1080,171);
  text("received: "+ inString,300,10);
  fill(color(255,255,255));
  square(100,300,50);
  square(50,350,50);square(100,350,50);square(150,350,50);
  square(100,400,50);
  if (keyPressed){
    fill(color(50,55,100));
    if(key == 'z'){
      port.write('z');
      circle(75,375,40);
    }
    if(key == 's'){
      port.write('s');
      circle(175,375,40);
    }
    if(key == 'q'){
      port.write('q');
      circle(125,425,40);
    }
    if(key == 'd'){
      port.write('d');
      circle(125,325,40);
    }
  }

}

void Carre(){port.write('c');}
void Circle(){port.write('o');}

void keyReleased(){
  port.write('x');
}

void serialEvent(Serial p)
{
  inString = p.readString();  
}

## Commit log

2021-04-21 Ajout des PCB bumpers sur le repo
    [BUMPER PCB.PCBDOC, BUMPER SCHEMA.SchDoc, LibrairieBumper.PcbLib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]
2021-04-21 Ajout PCB couronne et schéma Electrique
    [COURONNE PARTIE I PCB.PCBDOC, COURONNE PARTIE I SCHEMA.SchDoc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]
2021-04-22 Envoie des datasheets
2021-04-22 Envoie des dernières datasheets
2021-04-22 Enlèvement des README.txt et remplacement par des README.md
2021-04-22 dossiers renommés et ajout de fichiers
    [BUMPER PCB.PCBDOC, BUMPER SCHEMA.SchDoc, COURONNE PARTIE I PCB.PCBDOC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]
